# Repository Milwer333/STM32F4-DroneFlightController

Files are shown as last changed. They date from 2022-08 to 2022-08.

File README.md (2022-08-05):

# STM32F4-DroneFlightController
#### STM32F4-based drone flight controller designed from scratch.

This is my first ever attempt at designing and assembling a functional Flight Controller. The design is mostly a result of reverse-engineering of commertial products and deep research of the inner-workings of a drone.

**The board is a project for the university**. Designed in Altium Designer. Manufactured by JLCPCB. Assembled by hand.
___

#### The board consists of:
* STM32F405 microcontroller
* MPU-6000 6-axis IMU
* Hybrid construction (Flight Controller & Power Distribution Board)
* USB Type-C
* SBUS inverter
* Debugging tools
* Designed with Betaflight support in mind
* Test firmware (STM32CubeIDE)
___

**Disclaimer:** The flight controller prototype is currently missing the IMU unit due to global semiconductor shortage

BSD 3-Clause License - Copyright (c) 2022, Miłosz Werner - All rights reserved.

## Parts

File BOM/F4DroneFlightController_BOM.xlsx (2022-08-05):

Description | Designator | Value | Quantity | Comment | Link
SWITCH TACTILE SPST-NO 0.02A 15V | BOOT0, RESET |  | 2 | EVQQ2202W | https://www.mouser.pl/ProductDetail/Panasonic/EVQ-Q2202W?qs=WwqriLBepZu4g7g3xY%252BWKA%3D%3D
Capacitor | C5 | 2.2nF | 1 | Cap 0805
 | C3, C4, C6, C10, C11, C12, C13, C14 C16 | 0.1uF | 9
 | C7 | 1uF | 1
 | C1, C2 | 2.2uF | 2
 | C8, C9, C15 | 10uF | 3
Schottky Barrier Diode, 30 V, 2 uA, -55 to 150 degC, 3-Pin SOT23, RoHS, Tape and Reel | D1 |  | 1 | BAT54C | https://www.mouser.pl/ProductDetail/Diotec-Semiconductor/BAT54C?qs=OlC7AqGiEDmkBJ3TS7AJwQ%3D%3D
DIODE SCHOTTKY 40V 1A SMA | D2 |  | 1 | SS14 | https://www.mouser.pl/ProductDetail/onsemi-Fairchild/SS14?qs=mVVXn4M53U%252BvrBaFv5vr4w%3D%3D
Conv DC-DC 1V to 30V Non-Inv/Inv/Step Up/Step Down Single-Out 5V Micropower 8-Pin SOIC N Tube | IC1 |  | 1 | LT1110CS8-5#PBF | https://www.mouser.pl/ProductDetail/Analog-Devices/LT1110CS8-5PBF?qs=ytflclh7QUVB0t%252Bktc7oHA%3D%3D
CONN RCPT USB2.0 TYPEC 16POS | J1 |  | 1 | USB4085-GF-A | https://www.mouser.pl/ProductDetail/GCT/USB4085-GF-A?qs=KUoIvG%2F9Ilba1bQOahfWjw%3D%3D
SMD Shielded Tiny Power Inductor WE-TPC, L = 47.0 µH | L1 |  | 1 | PM528S-470-RC | https://www.mouser.pl/ProductDetail/Bourns/PM528S-470-RC?qs=trOM%252BqvATNUGwISk3Gc91w%3D%3D
LED | LED1, LED2 |  | 2 | LED 0805
PNP Silicon AF Transistor, 45 V VCEO, 100 mA IC, SOT23, Reel, Green | Q1 |  | 1 | BC857C | https://www.mouser.pl/ProductDetail/Diotec-Semiconductor/BC857C?qs=OlC7AqGiEDnnDRsXkzRNsA%3D%3D
Resistor | R10, R11 | 22 | 2 | Res 0805
 | R9 | 220 | 1
 | R7, R8 | 1K | 2
 | R6 | 4.7K | 1
 | R12 | 5.1K | 1
 | R1, R2, R3, R4, R5 | 10K | 5
 | R13 | 1M | 1
ARM Cortex-M4 32-bit MCU+FPU, 210 DMIPS, 1024 kB Flash, 192 kB Internal RAM, 51 I/Os, 64-pin LQFP, -40 to 85 degC, Tray | U1 |  | 1 | STM32F405RGT6 | https://www.mouser.pl/ProductDetail/STMicroelectronics/STM32F405RGT6?qs=Z8%252BeY1k3TIKgj7QWsYGpQw%3D%3D
3-Axis Gyroscope 3-Axis Accelerometer Motion Processing Unit with I2C and SPI, 2.5, 3 or 3.3 V, -40 to 85 degC, 24-Pin QFN, RoHS, Tape and Reel | U2 |  | 1 | MPU-6000 | https://www.mouser.pl/ProductDetail/TDK-InvenSense/MPU-6000?qs=u4fy%2FsgLU9NMLimeLRzXLA%3D%3D
Low-Dropout Positive Fixed Voltage Regulator, 1 A, 3.3 V Output Voltage, 0 to 125 degC, 4-Pin SOT-223 (318H-01), Pb-Free, Tape and Reel | U3 |  | 1 | NCP1117ST33T3G | https://www.mouser.pl/ProductDetail/onsemi/NCP1117ST33T3G?qs=Gev%252BmEvV0iZb%2FE8ahUDx3w%3D%3D
CERAMIC RES 8.0000MHZ 33PF SMD | Y1 | 8MHz | 1 | CSTNE8M00GH5C000R0 | https://www.mouser.pl/ProductDetail/Murata-Electronics/CSTNE8M00GH5C000R0?qs=y6ZabgHbY%252ByuG8XwUR67qA%3D%3D

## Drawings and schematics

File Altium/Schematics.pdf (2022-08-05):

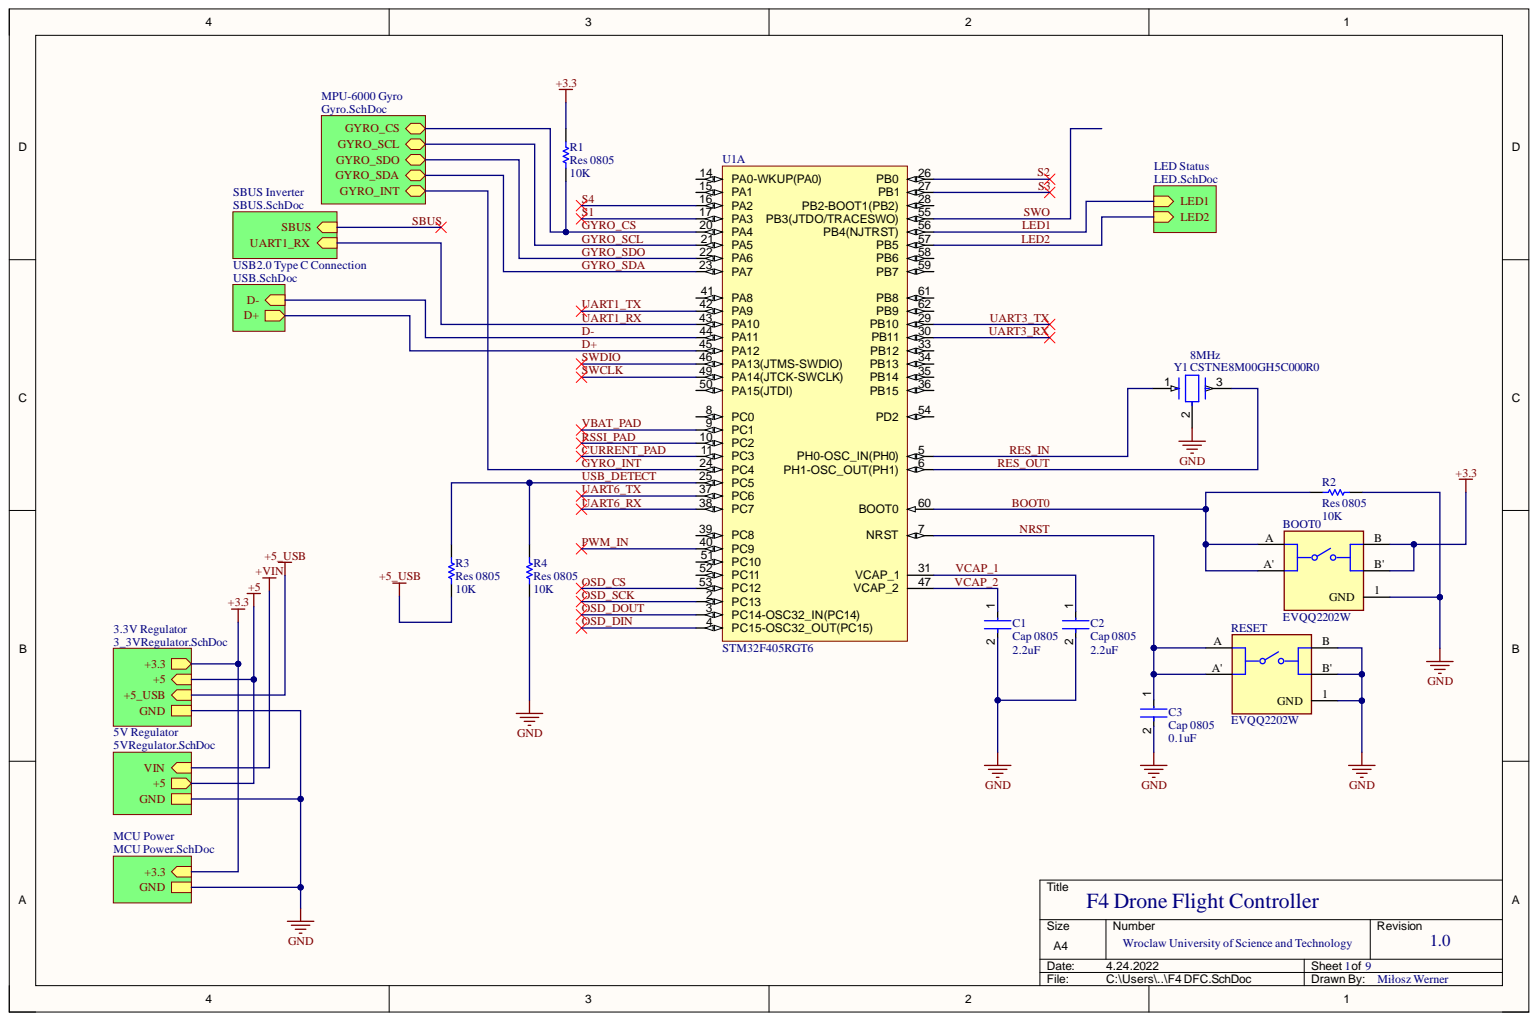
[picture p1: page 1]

S | S4 G YRO _CS

S1UA G YRO _SCL | | L E D 2

i o n | G YRO _SD O

G YRO _SD A

RT 1 _T X
U A RT 1 _RX
D -
D +
SW D I O SWCL K VBAT _PA D RSSI_ PA D CURRE N T _PA D G YRO _IN T

8 | | RES_ IN
9 1 1 | 5

7 | NRS T | BO O T

VCAP_ 1

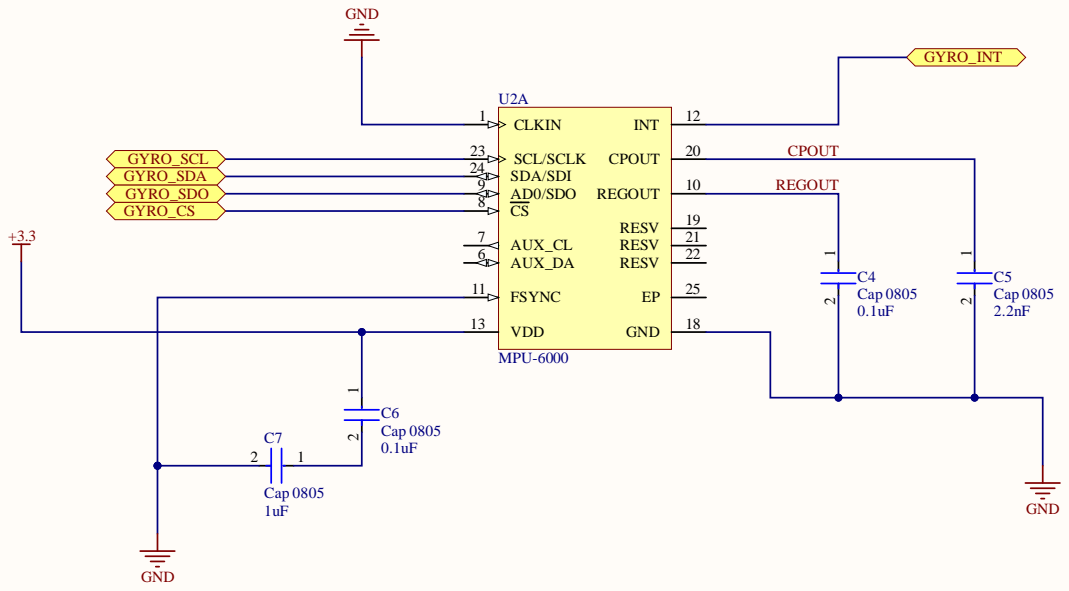
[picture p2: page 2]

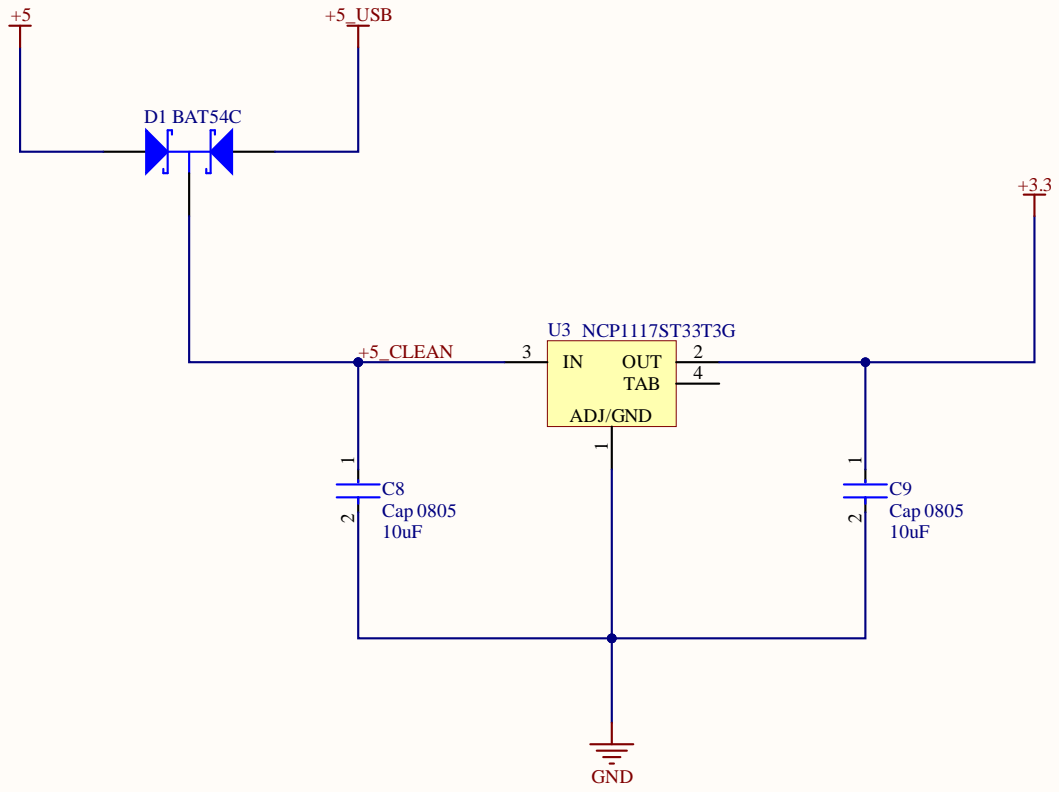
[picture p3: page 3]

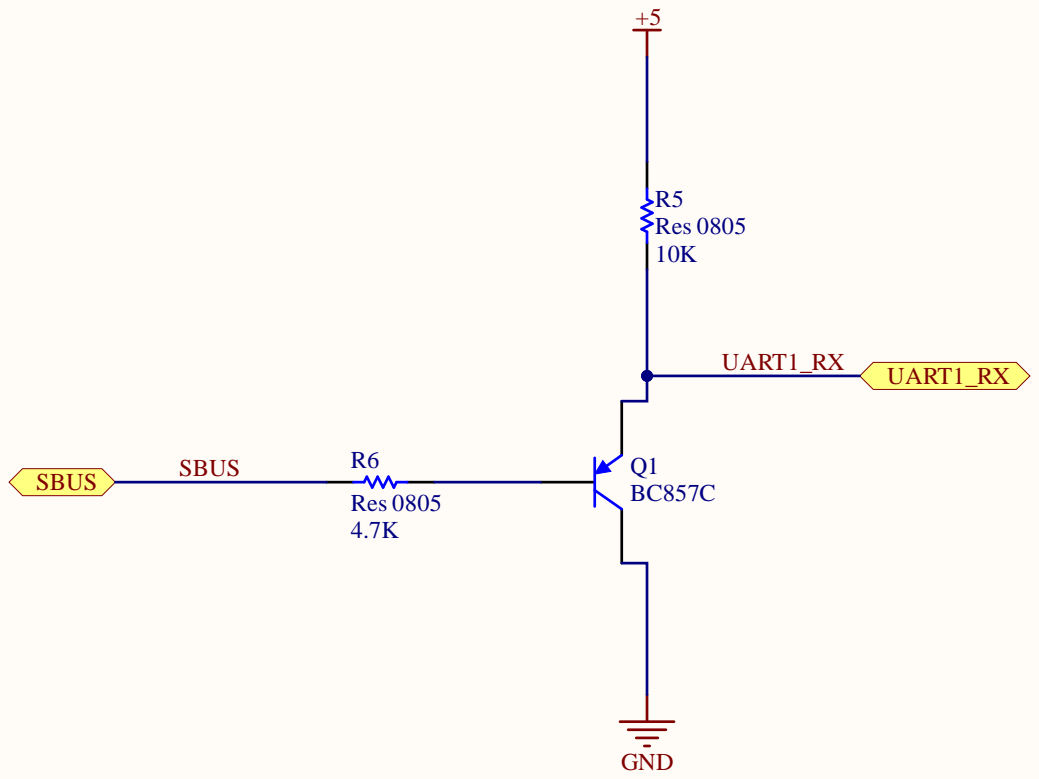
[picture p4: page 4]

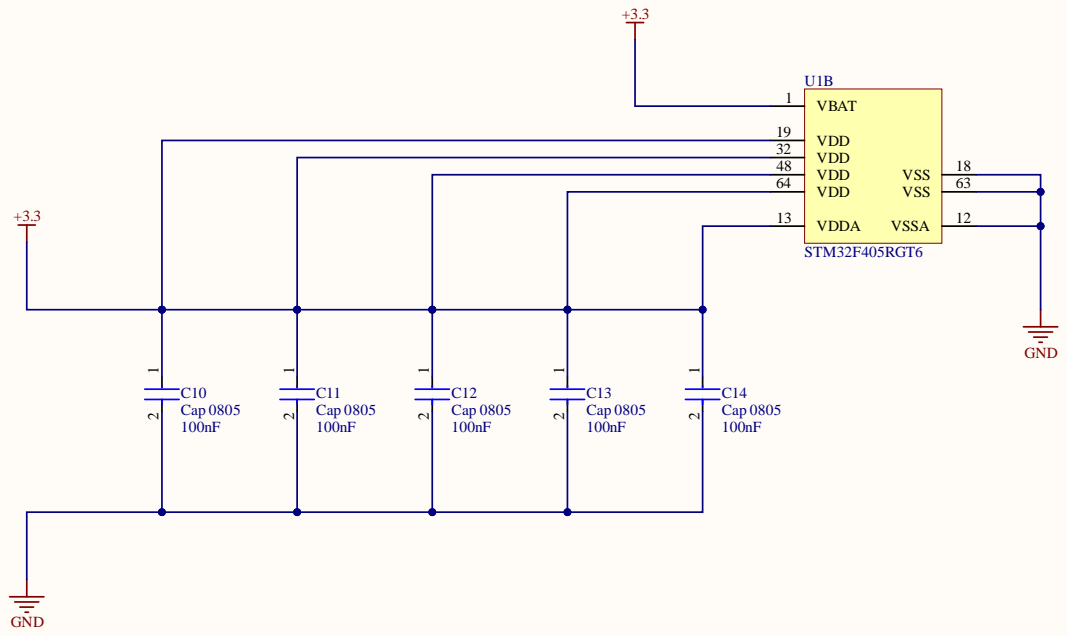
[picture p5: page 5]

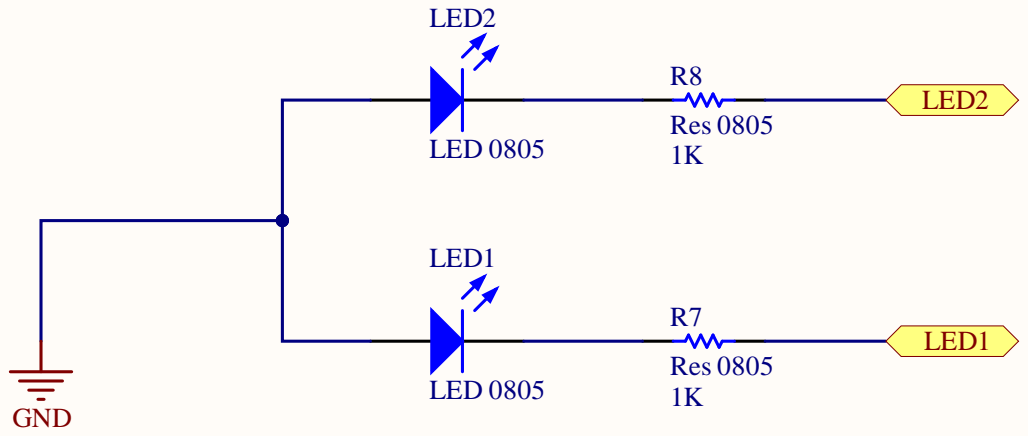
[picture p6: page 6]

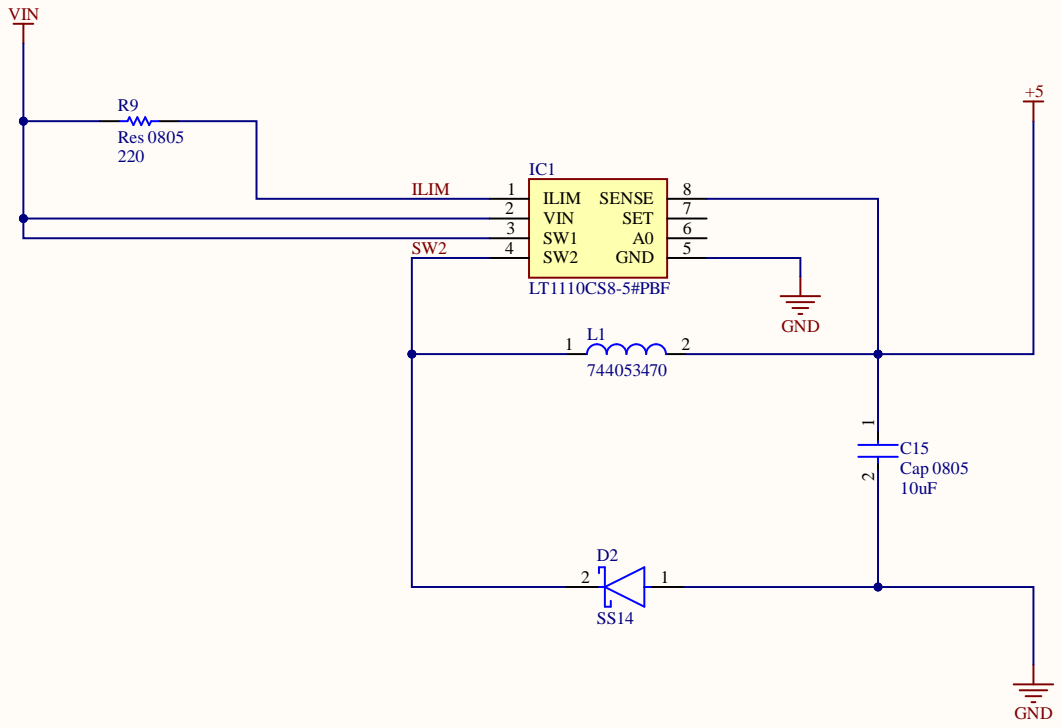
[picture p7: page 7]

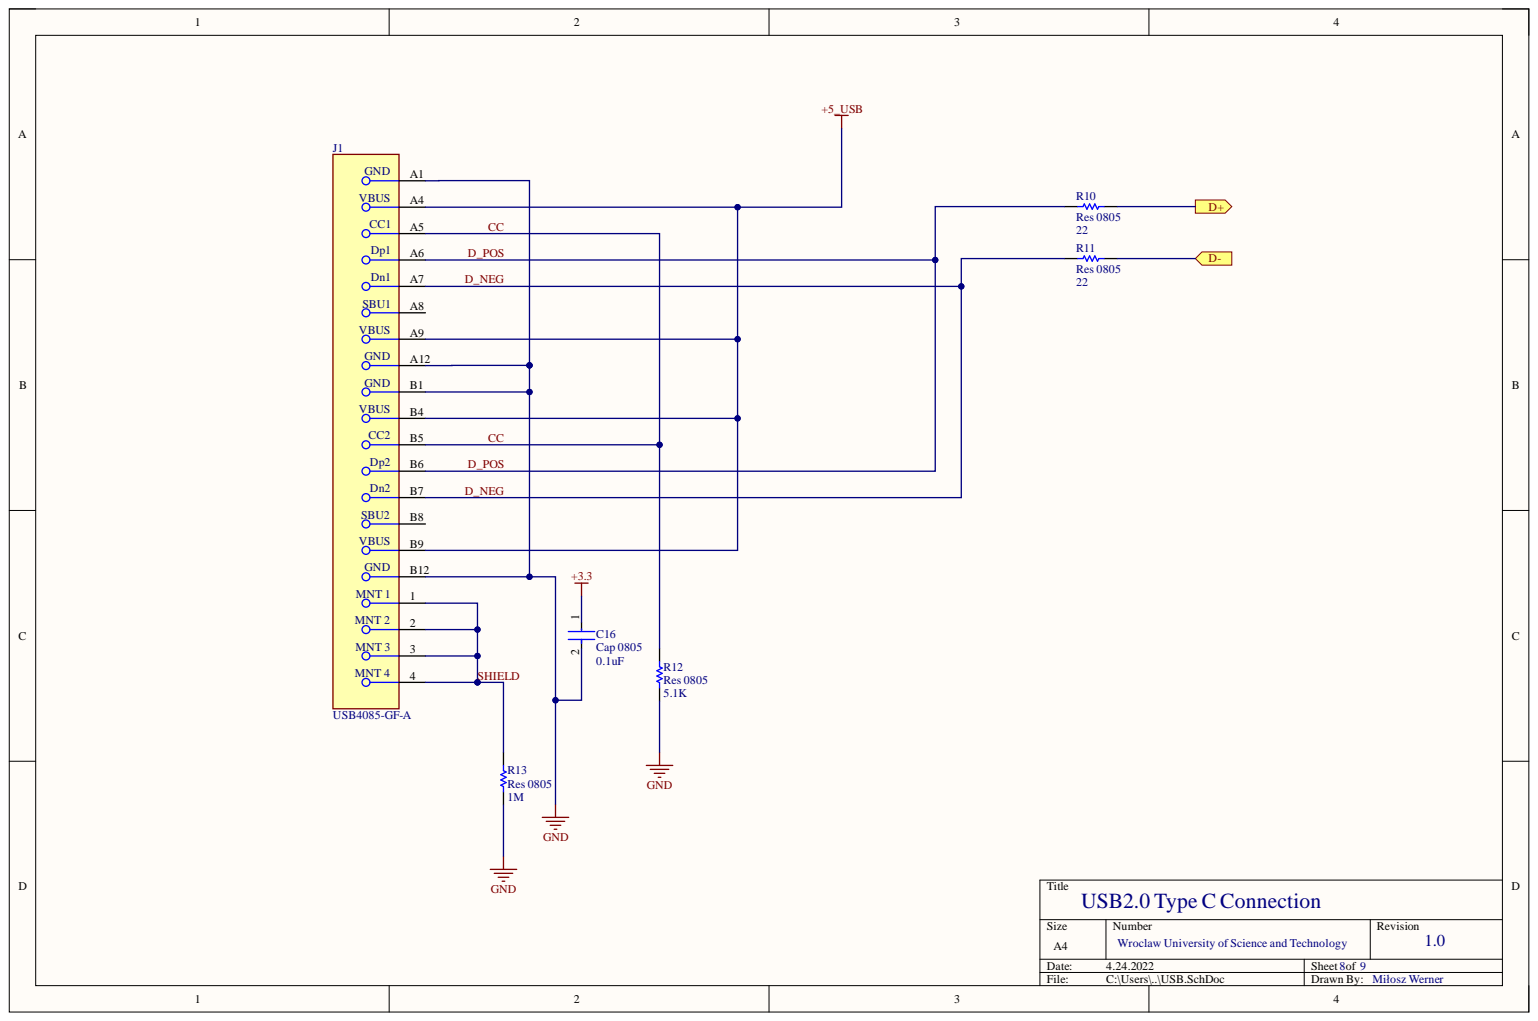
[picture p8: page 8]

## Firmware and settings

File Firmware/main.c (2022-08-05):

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
/* Includes ------------------------------------------------------------------*/
#include "main.h"
#include "usb_device.h"

SPI_HandleTypeDef hspi1;

TIM_HandleTypeDef htim2;
TIM_HandleTypeDef htim3;

UART_HandleTypeDef huart1;
UART_HandleTypeDef huart3;
UART_HandleTypeDef huart6;

void SystemClock_Config(void);
static void MX_GPIO_Init(void);
static void MX_SPI1_Init(void);
static void MX_TIM2_Init(void);
static void MX_TIM3_Init(void);
static void MX_USART1_UART_Init(void);
static void MX_USART3_UART_Init(void);
static void MX_USART6_UART_Init(void);
/**
 * @brief  The application entry point.
 * @retval int
 */
int main(void) {
	/* MCU Configuration--------------------------------------------------------*/

	/* Reset of all peripherals, Initializes the Flash interface and the Systick. */
	HAL_Init();

	/* Configure the system clock */
	SystemClock_Config();

	/* Initialize all configured peripherals */
	MX_GPIO_Init();
	MX_SPI1_Init();
	MX_TIM2_Init();
	MX_TIM3_Init();
	MX_USART1_UART_Init();
	MX_USART3_UART_Init();
	MX_USART6_UART_Init();
	MX_USB_DEVICE_Init();
	/* USER CODE BEGIN 2 */

	HAL_GPIO_WritePin(GPIOB, GPIO_PIN_5, 1);

	HAL_TIM_PWM_Start(&htim2, TIM_CHANNEL_3); // S4
	HAL_TIM_PWM_Start(&htim2, TIM_CHANNEL_4); // S1
	HAL_TIM_PWM_Start(&htim3, TIM_CHANNEL_3); // S2
	HAL_TIM_PWM_Start(&htim3, TIM_CHANNEL_4); // S3

	HAL_TIM_PWM_Start(&htim3, TIM_CHANNEL_1); // RED PWM LED

	uint8_t red_intensity = 0;
	uint8_t condition = 0;
	uint8_t led_intensity = 0;

	/* USER CODE END 2 */

	/* Infinite loop */
	/* USER CODE BEGIN WHILE */
	while (1) {
		/* USER CODE END WHILE */

		/* USER CODE BEGIN 3 */

		htim3.Instance->CCR1 = red_intensity;
		red_intensity += 20;
		if (red_intensity > 100) {
			red_intensity = 0;
		}

		switch (condition) {
		case 0: {

			led_intensity += 5;
			if (led_intensity > 100) {
				led_intensity = 0;
				condition = 1;
			}
			htim3.Instance->CCR3 = led_intensity;
			break;
		}
		case 1: {

			led_intensity += 5;
			if (led_intensity > 100) {
				led_intensity = 0;
				condition = 2;

			}
			htim3.Instance->CCR4 = led_intensity;
			break;
		}
		case 2: {

			led_intensity += 5;
			if (led_intensity > 100) {
				led_intensity = 0;
				condition = 3;

			}
			htim2.Instance->CCR3 = led_intensity;
			break;
		}
		case 3: {

			led_intensity += 5;
			if (led_intensity > 100) {
				led_intensity = 0;
				condition = 0;

			}

			htim2.Instance->CCR4 = led_intensity;
			break;
		}
		}

		HAL_Delay(100);
	}
	/* USER CODE END 3 */
}

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

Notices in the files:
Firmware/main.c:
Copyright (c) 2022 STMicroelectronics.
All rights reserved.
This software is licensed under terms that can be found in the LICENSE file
